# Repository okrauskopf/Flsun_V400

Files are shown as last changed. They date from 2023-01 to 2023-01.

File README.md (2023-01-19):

## A common issue with Flsun V400  
  
Problems with your Flsun V400 nozzle sometimes scraping or crashing into filament -&gt; layer shifts -&gt; spaghetti?  
  
If you skip one of the items in the list, or even just do one of them slightly haphazardly, you will probably still have problems.   
  
## Guide

1 - Make sure all screws are tight on your printer. Stepper motors, extruder block, extruder/arm connectors, bed, the three columns and so on. 

2 - Tighten all three belts to be exactly equally tight. With the extruder at the very top adjust the belt tightening knobs to tune them all to somewhere between 45-50Hz, but exactly the same all three! Either print out a belt tension gauge or use a guitar tuning app on your mobile phone listening to the sounds from the belts when you pluck them. When done make sure you tighten all the screws for the belts.  
    
3 - Do Klipper probe calibration https://www.klipper3d.org/Probe_Calibrate.html  
  
4 - Do the Delta, Bed Mesh and Z height calibrations and so on as described in the Flsun V400 manual. Do it when the bed has been hot for 15 minutes so it is evenly heated.  
  
5 - Calibrate E-steps and add the result into the printer.cfg on your SpeederPad <a href="https://ellis3dp.com/Print-Tuning-Guide/articles/extruder_calibration.html"> with clear steps in this guide</a>   
  
6 - Calibrate Extrusion Multiplier (Flow) and add the result in Cura, <a href=https://ellis3dp.com/Print-Tuning-Guide/articles/extrusion_multiplier.html>with yet another great guide by Ellis</a>. This setting is per filament type. PETG and PLA can need different settings, but different makes _can_ differ also. Important to have this set correctly for every filament you use and not have over extrusion.
  
7 - Check that you got the bed height 100% set right <a href="https://ellis3dp.com/Print-Tuning-Guide/articles/first_layer_squish.html">with this great guide</a>. Also do a test print of a first layer while you fine tune Z "live" under the pad's "Fine tuning" while printing.  
  
If you have carefully done each step above, and with a bit of luck, the printer will now work fine. If not try this: Download <a href="Updated%20config%20for%20Cura%20-%20Flsun%20V400%20(v1.0).zip?raw=true">this updated Flsun V400 zip file for Cura (zip v1.0)</a> and install it as described in the readme file inside it. Do not forget to change to your calibrated flow values in Cura after installing this! 

## These are the changes in the above zip done to the Flsun's stock V400 files for Cura  

- Infill changed to Gyroid
- Retraction Z hop raised from 0.3 to 0.8
- Combing off (can make prints take a longer time though, you can experiment with it on or off)
- Material Flow (A.K.A. Extrusion Multiplier) set to a better default value at 98,5 instead of 100 but you must still calibrate for your filament and change in Cura after adding these files! 
- BED_MESH_PROFILE LOAD=default added to the start code
- Flow compensation added for first layer above sparse infill to prevent blobs at higher speeds that the nozzle then can hit. Both threshold corrected and flow increase added. Might need tweaking for ordinary bridges but so far very good.
- All bed and nozzle temperatures are taken from the currently chosen filament instead of fixed values. So changing filament in Cura actually does something.
- Fan Speed takes its speed value from currently chosen filament instead of a fixed value
- All speeds now automatically get values derived from the main printing speed instead of fixed individual values. Next step is to take the speed values from the filaments so TPU or PLA and so on to get speeds correctly adjusted automatically. 
- The first extruder move from home is down to the edge of the bed instead of center to prevent filament drops in the bed center, changed in the start code  

Nothing else is changed from the original Flsun stock file that you received on the USB stick. 
  
Thanks to everyone contributing info for the V400!!
  
## More info  
  
For further info check out Guilouz very thorough guide https://github.com/Guilouz/Klipper-Flsun-Speeder-Pad

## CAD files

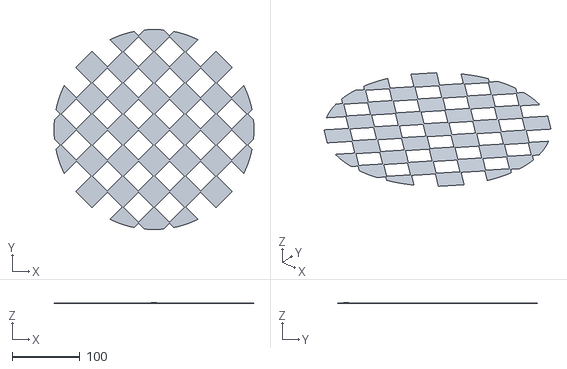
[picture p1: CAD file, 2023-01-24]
Bed Mesh 7x7.stl
295.0 x 295.0 x 0.5

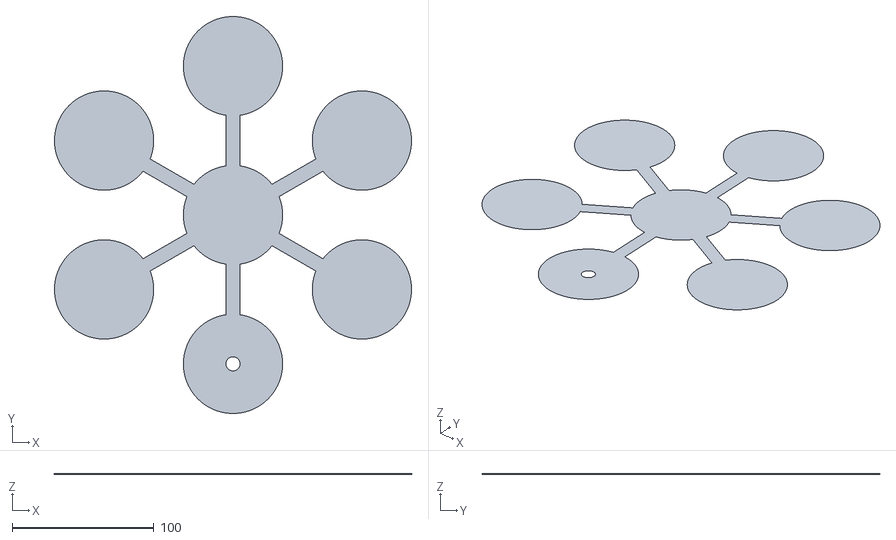
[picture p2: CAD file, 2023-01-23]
Mesh Test.stl
251.9 x 280.0 x 0.2

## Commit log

2022-12-14 Update README.md
    v0.5
    Added material_flow at 98,5%
    Fixed ironing speed calculation to work with the higher top/bottom speed
2023-01-19 Probe cal
